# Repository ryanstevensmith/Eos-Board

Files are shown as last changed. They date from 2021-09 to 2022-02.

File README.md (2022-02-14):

# Eos-Board
 The Eos altimeter board for altimeter development within HRG
 
 Due to be built and tested in October 2021
 
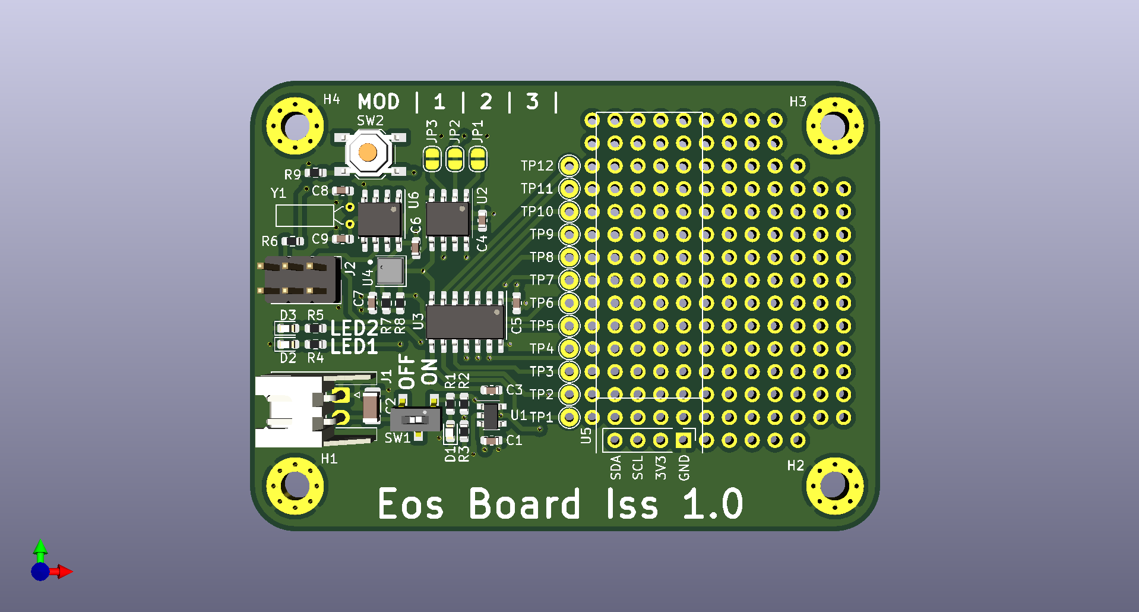
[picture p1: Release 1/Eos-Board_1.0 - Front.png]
image of Board front
 
 
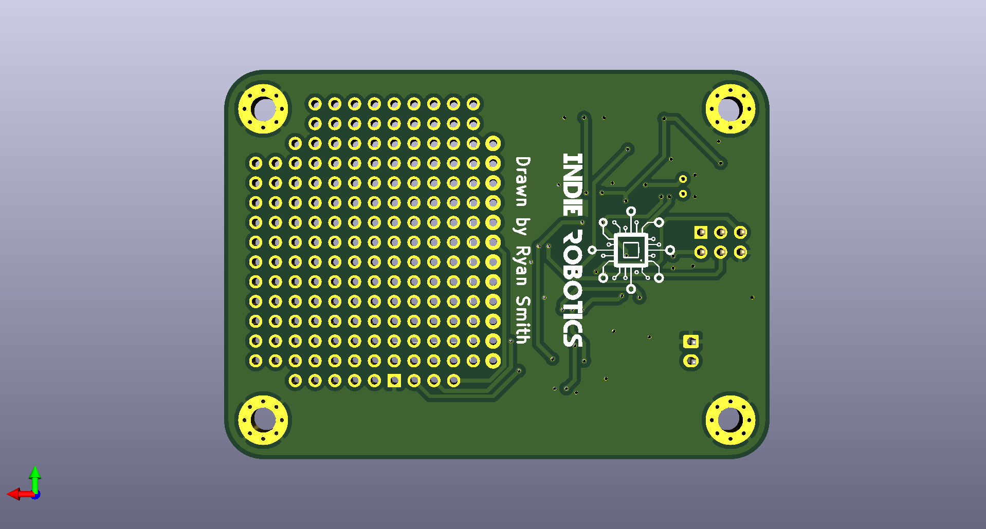
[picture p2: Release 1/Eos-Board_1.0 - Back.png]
image of Board Back
 
 
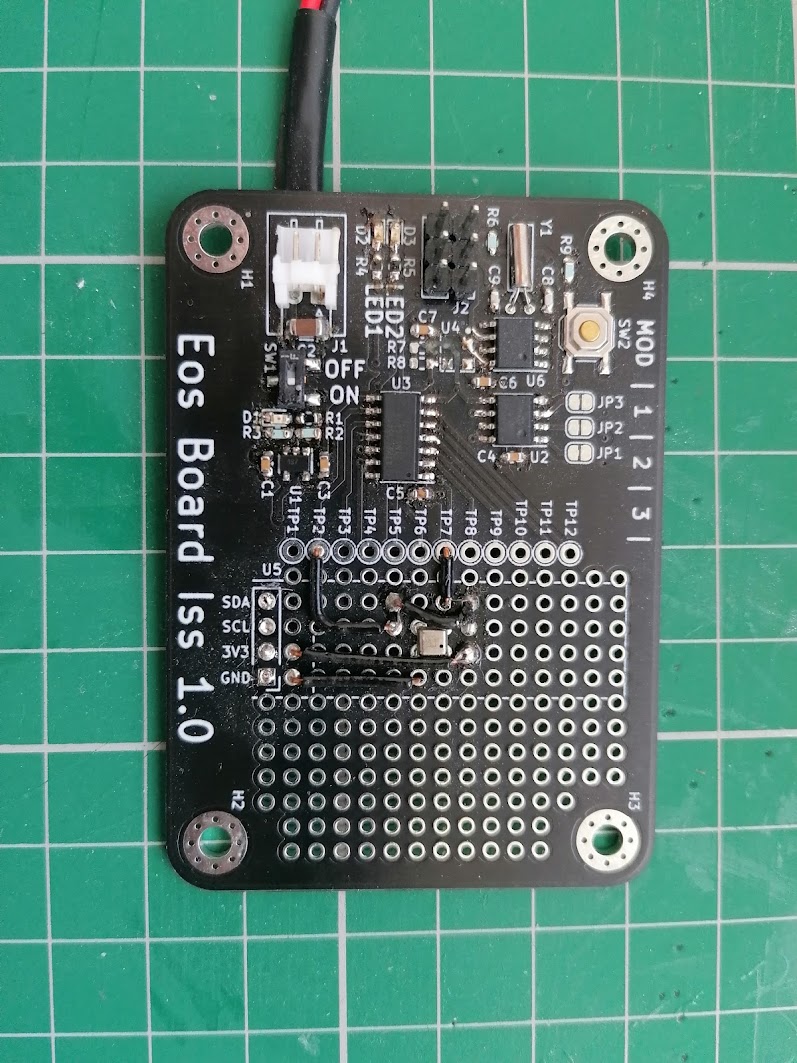
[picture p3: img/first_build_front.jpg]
image of the built board front
 

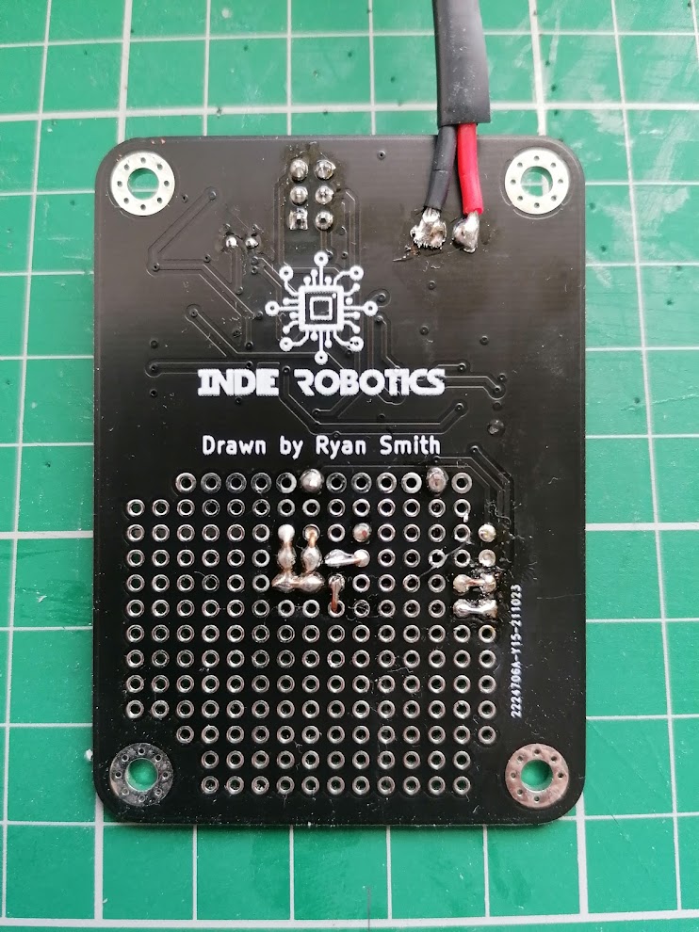
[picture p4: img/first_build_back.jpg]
image of the built board back
 

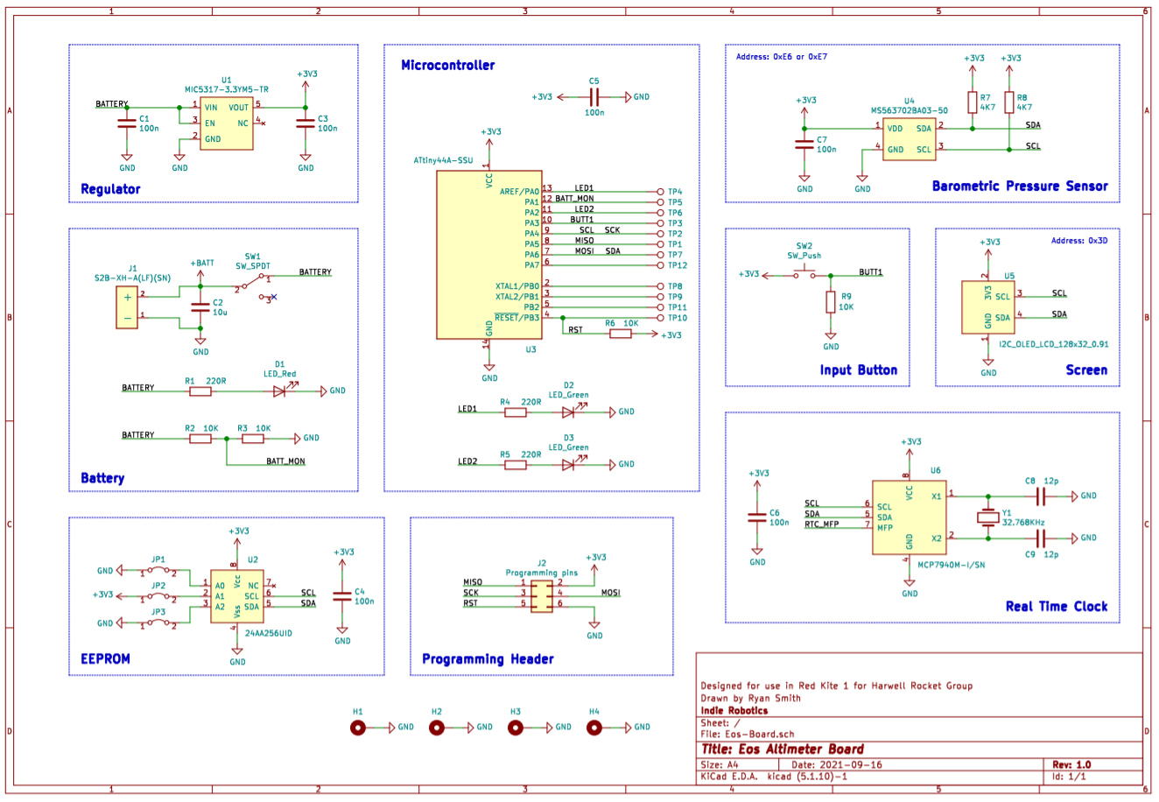
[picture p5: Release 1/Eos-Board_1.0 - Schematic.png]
Schematic Design


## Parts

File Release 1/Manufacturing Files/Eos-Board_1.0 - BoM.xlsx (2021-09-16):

Source: | C:\Users\rsmit\Documents\Rocket Group\Eos-Board\working\Eos-Board.sch
Date: | 2021-09-16
Tool: | Eeschema (5.1.10)-1
Generator: | C:\Program Files\KiCad\bin\scripting\plugins/bom_csv_grouped_by_value.py
Component Count: | 39
Collated Components:
Item | Qty | Reference(s) | Value | Footprint | Part Number | Manufacturer | Description | Datasheet
1 | 6 | C1, C3, C4, C5, C6, C7 | 100n | C_0603_1608Metric | C0603C104J5RACTU | KEMET | 100n, 0603, X7R, 50V | https://api.kemet.com/component-edge/download/specsheet/C0603C104J5RACTU.pdf
2 | 1 | C2 | 10u | C_1206_3216Metric | C1206C106M3PACTU | KEMET | 10u, 1206, X5R, 25V | https://api.kemet.com/component-edge/download/specsheet/C1206C106M3PACTU.pdf
3 | 2 | C8, C9 | 12p | C_0603_1608Metric | C0603C120K5RACTU | KEMET | 10p, 0603, X7R, 50V | https://api.kemet.com/component-edge/download/specsheet/C0603C120K5RACTU.pdf
4 | 1 | D1 | LED_Red | LED_0603_1608Metric | APT1608SRCPRV | Kingbright | Red 0603 LED | https://www.mouser.co.uk/datasheet/2/216/APT1608SRCPRV-226086.pdf
5 | 2 | D2, D3 | LED_Green | LED_0603_1608Metric | APT1608SGC | Kingbright | Green 0603 LED | https://www.mouser.co.uk/datasheet/2/216/APT1608SGC-32861.pdf
7 | 1 | J1 | S2B-XH-A(LF)(SN) | S2B-XH-A(LF)(SN) | S2B-XH-A(LF)(SN) | JST | CONN HEADER R/A 2POS 2.5MM | https://www.te.com/commerce/DocumentDelivery/DDEController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
10 | 3 | R1, R4, R5 | 220R | R_0603_1608Metric | CRCW0603220RFKEAHP | Vishay | 220R, 0603, 1%, 0.33W | https://www.vishay.com/docs/20043/crcwhpe3.pdf
11 | 4 | R2, R3, R6, R9 | 10K | R_0603_1608Metric | CRCW060310K0FKEAHP | Vishay | 10K, 0603, 1%, 0.33W | https://www.vishay.com/docs/20043/crcwhpe3.pdf
12 | 2 | R7, R8 | 4K7 | R_0603_1608Metric | CRCW06034K70FKEAHP | Vishay | 4K7, 0603, 1%, 0.33W | https://www.vishay.com/docs/20043/crcwhpe3.pdf
13 | 1 | SW1 | SW_SPDT | CAS-120-B-type | CAS-120TB | NIDEC | Slide Switch, SPDT, On-On, Surface Mount, CAS Series, 100 mA | https://www.farnell.com/datasheets/2705275.pdf
14 | 1 | SW2 | SW_Push | SW_SPST_TL3342 | TL3342F160QG | E-Switch | Tactile Switches 4.9 X 4.9MM 160G | https://www.mouser.co.uk/datasheet/2/140/TL3342-2065746.pdf
15 | 1 | U1 | MIC5317-3.3YM5-TR | SOT-23-5 | MIC5317-3.3YM5-TR | Microchip | Fixed LDO Voltage Regulator, 2.5V to 6V, 155mV drop, 3.3V/150mA out, SOT-23-5 | http://ww1.microchip.com/downloads/en/DeviceDoc/MIC5317.pdf
16 | 1 | U2 | 24AA256UID | SOIC-8_3.9x4.9mm | 24AA256UID-I/SN | Microchip | EEPROM, 256 Kbit, 32K x 8bit, Serial I2C (2-Wire), 400 kHz, SOIC, 8 Pins | https://4donline.ihs.com/images/VipMasterIC/IC/MCHP/MCHP-S-A0002344565/MCHP-S-A0002344565-1.pdf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
17 | 1 | U3 | ATtiny44A-SSU | SOIC-14_3.9x8.7mm | ATTINY44A-SSU | Microchip | 8 Bit MCU, Low Power High Performance, AVR ATtiny Family ATtiny44 Series Microcontrollers, 20 MHz | http://ww1.microchip.com/downloads/en/DeviceDoc/doc8183.pdf
18 | 1 | U4 | MS563702BA03-50 | MS5637-02BA03 | MS563702BA03-50 | TE | Low Voltage Barometric Pressure Sensor | https://www.te.com/commerce/DocumentDelivery/DDEController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
19 | 1 | U5 | I2C_OLED_LCD_128x32_0.91 | I2C_128x32_OLED_LCD | n/a | n/a | I2C 0.91" LCD OLED screen with SSD1306 driver | https://www.ebay.co.uk/itm/IIC-I2C-0-91-inch-128x32-White-OLED-LCD-Display-Module-3-3v-5v-FOR-AVR-Arduino/313145258645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
20 | 1 | U6 | MCP7940M-I/SN | SOIC-8_3.9x4.9mm_P1.27mm | MCP7940M-I/SN | Microchip | RTC IC, Date Time Format (Date/Month/Year hh:mm:ss), I2C, 1.8 V to 5.5 V, MSOP-8 | http://ww1.microchip.com/downloads/en/devicedoc/20002292b.pdf
21 | 1 | Y1 | 32.768KHz | Crystal_DS26_D2.0mm_L6.0mm_Horizontal | R26-32.768- 12.5 | RALTRON | Crystal, 32.768 kHz, Radial, 6.2mm x 2mm Dia, 12.5 pF, 20 ppm, R26 Series | http://www.ramitechnology.com/products/spec/crystal/crystal-r38_26_145.pdf

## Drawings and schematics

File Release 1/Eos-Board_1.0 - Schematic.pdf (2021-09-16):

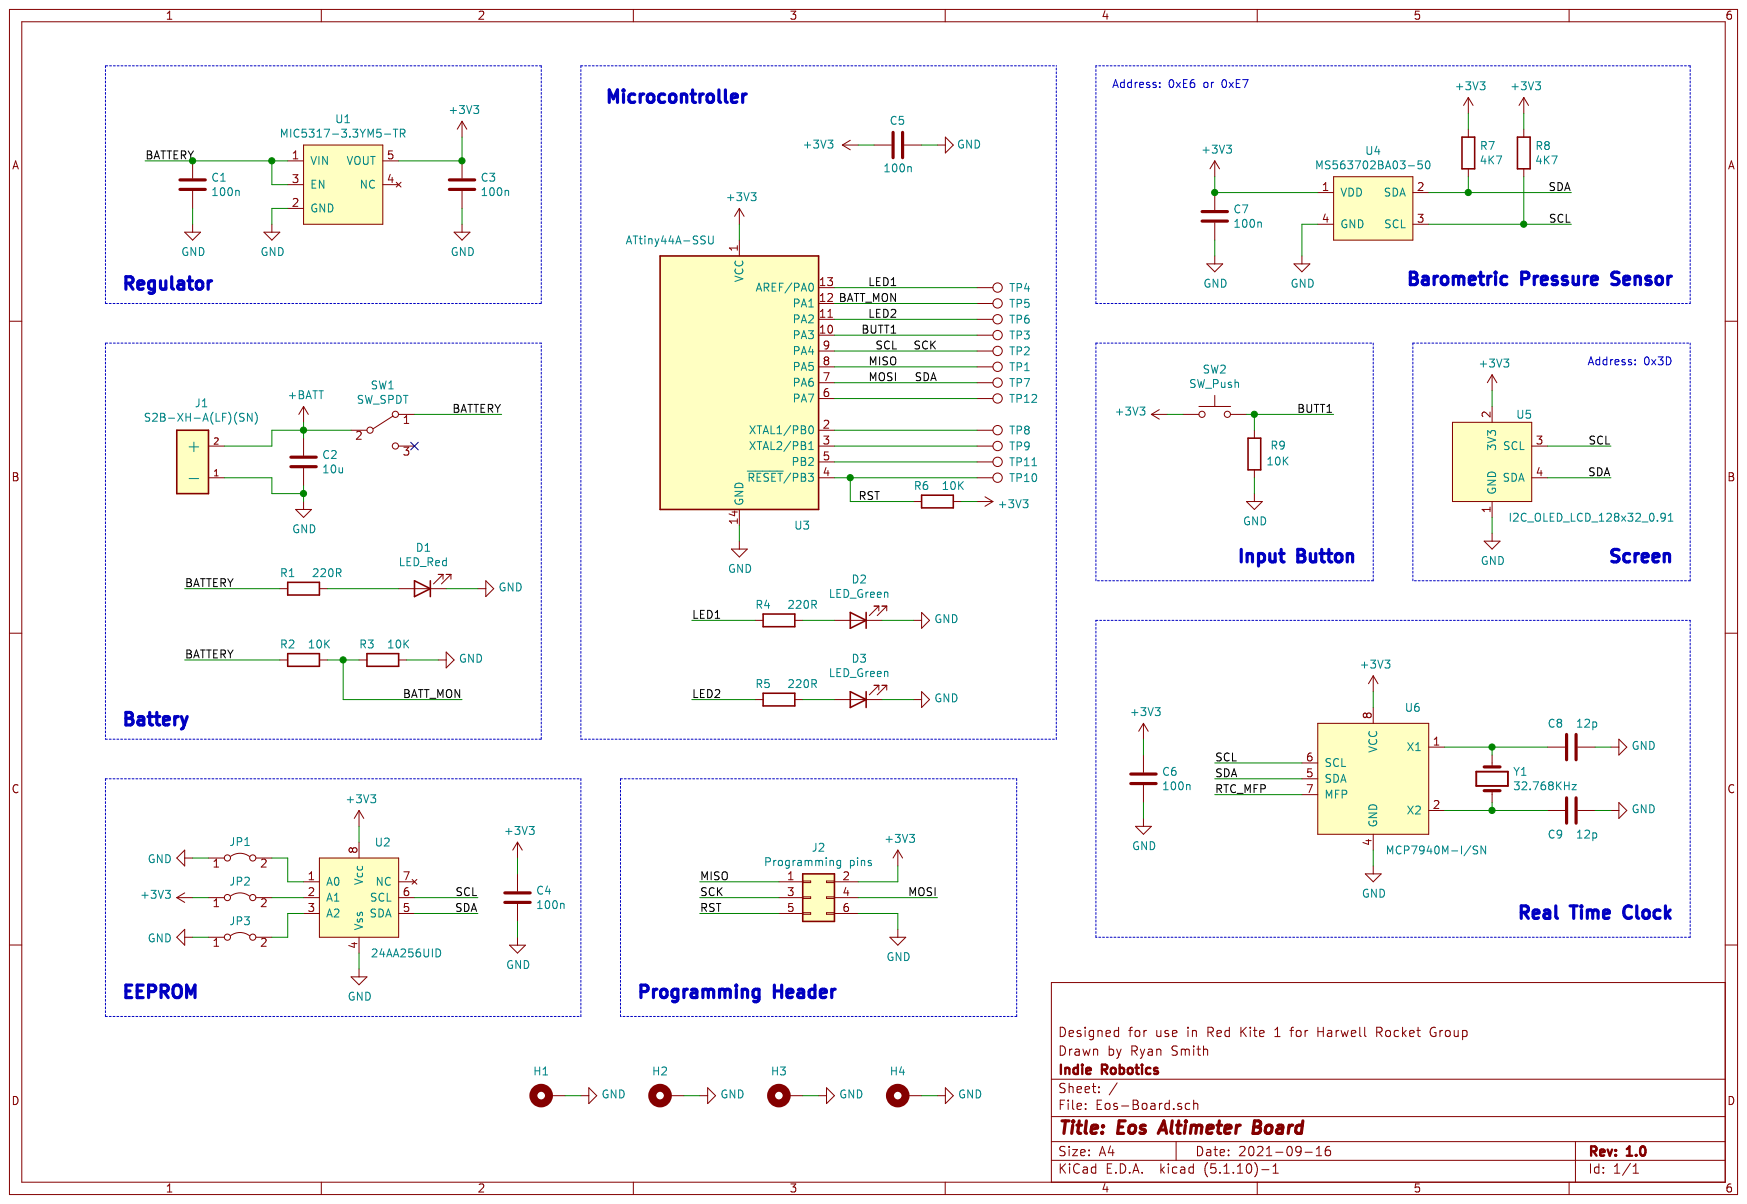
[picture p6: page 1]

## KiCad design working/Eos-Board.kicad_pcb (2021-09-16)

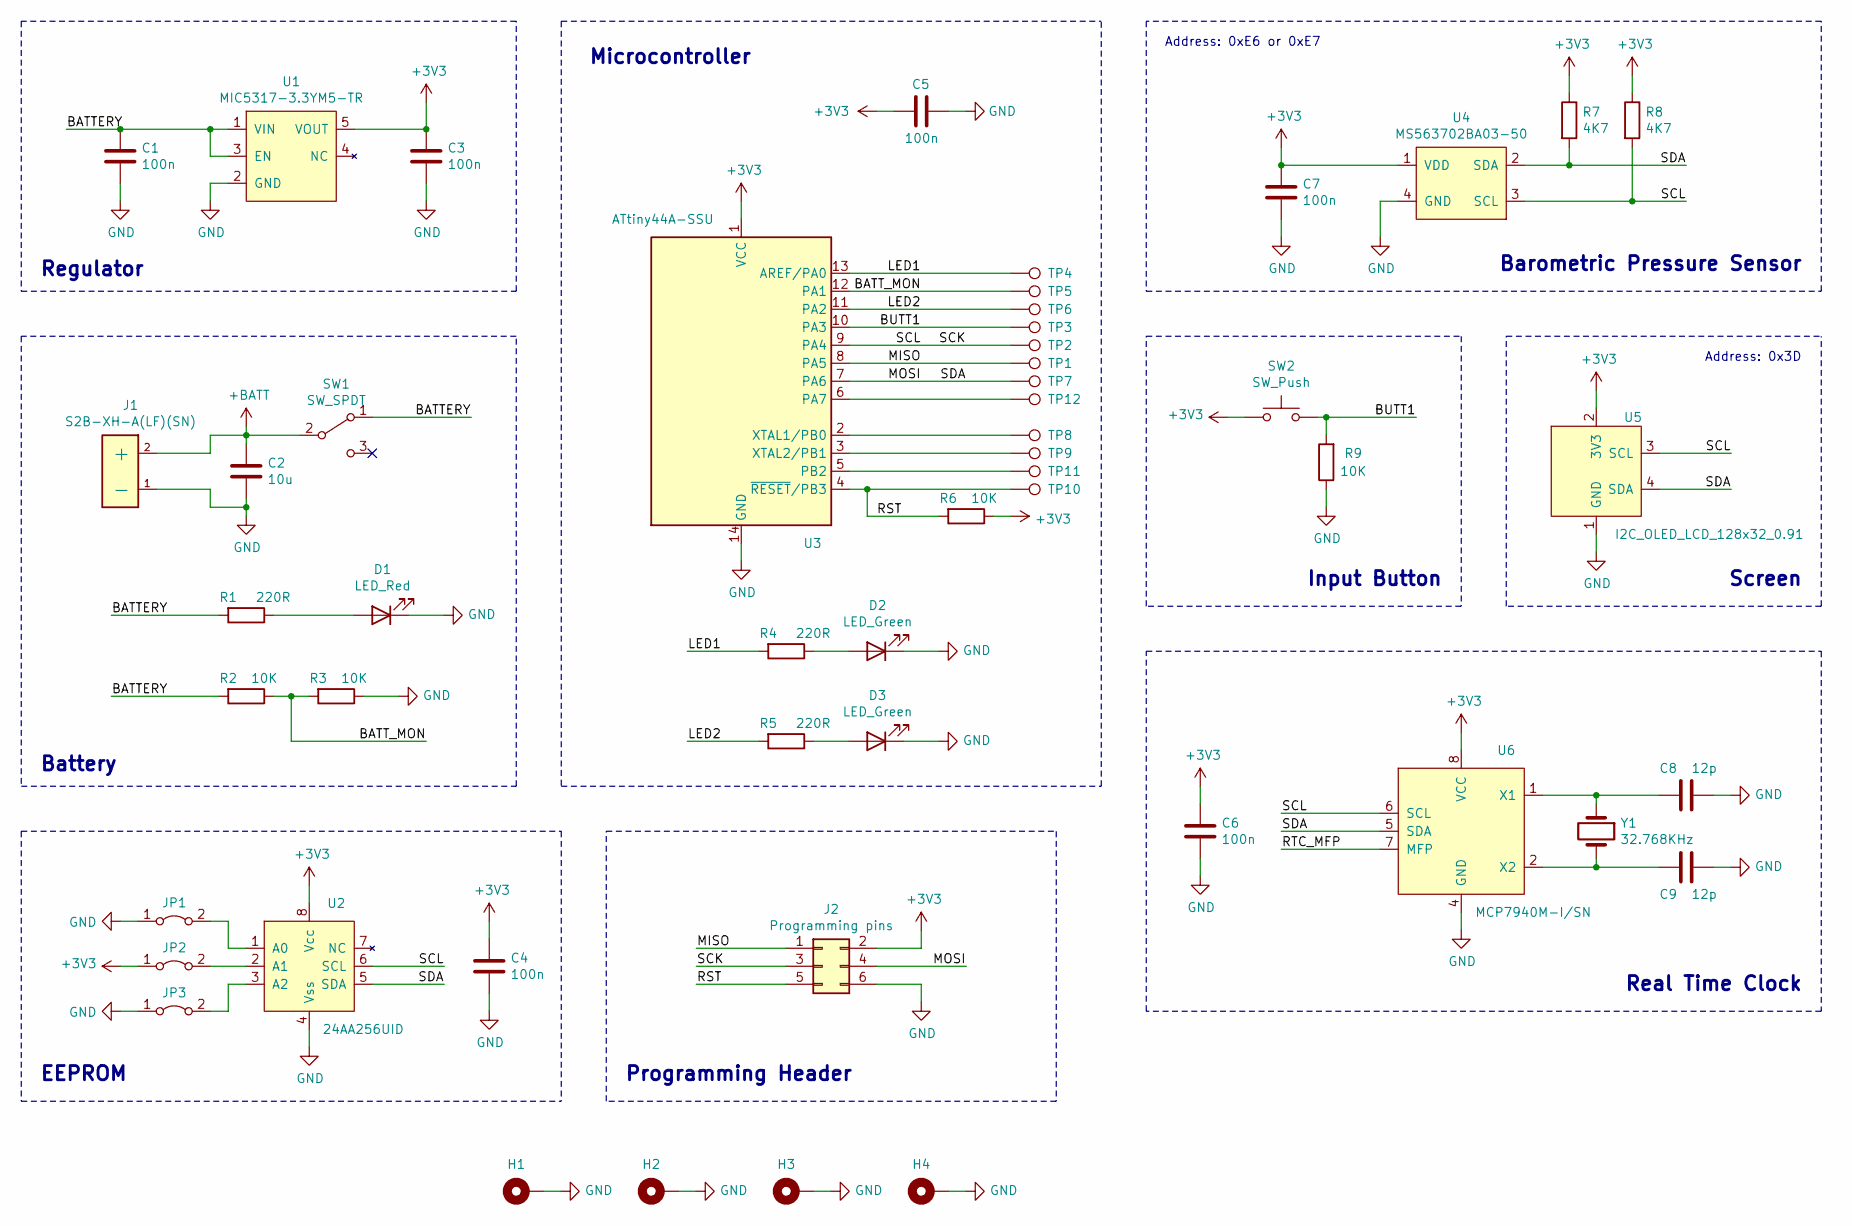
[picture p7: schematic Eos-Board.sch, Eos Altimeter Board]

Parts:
C1, C3, C4, C5, C6, C7: 100n; C_0603_1608Metric; Part Number C0603C104J5RACTU
C2: 10u; C_1206_3216Metric; Part Number C1206C106M3PACTU
C8, C9: 12p; C_0603_1608Metric; Part Number C0603C120K5RACTU
D1: LED_Red; LED_0603_1608Metric; Part Number APT1608SRCPRV
D2, D3: LED_Green; LED_0603_1608Metric; Part Number APT1608SGC
H1, H2, H3, H4: MountingHole_Pad; MountingHole_3.2mm_M3_Pad_Via
J1: S2B-XH-A(LF)(SN); Part Number S2B-XH-A(LF)(SN)
J2: Programming pins; PinHeader_2x03_P2.54mm_Vertical
JP1, JP2, JP3: Jumper_2_Bridged; SolderJumper-2_P1.3mm_Bridged_RoundedPad1.0x1.5mm
R1, R4, R5: 220R; R_0603_1608Metric; Part Number CRCW0603220RFKEAHP
R2, R3, R6, R9: 10K; R_0603_1608Metric; Part Number CRCW060310K0FKEAHP
R7, R8: 4K7; R_0603_1608Metric; Part Number CRCW06034K70FKEAHP
SW1: SW_SPDT; CAS-120-B-type; Part Number CAS-120TB
SW2: SW_Push; SW_SPST_TL3342; Part Number TL3342F160QG
TP1, TP2, TP3, TP4, TP5, TP6, TP7, TP8, TP9, TP10, TP11, TP12: TestPoint; TestPoint_THTPad_D2.0mm_Drill1.0mm
U1: MIC5317-3.3YM5-TR; SOT-23-5; Part Number MIC5317-3.3YM5-TR
U2: 24AA256UID; SOIC-8_3.9x4.9mm_P1.27mm; Part Number 24AA256UID-I/SN
U3: ATtiny44A-SSU; SOIC-14_3.9x8.7mm_P1.27mm
U4: MS563702BA03-50; MS5637-02BA03; Part_Number MS563702BA03-50
U5: I2C_OLED_LCD_128x32_0.91; I2C_128x32_OLED_LCD; Part Number n/a
U6: MCP7940M-I/SN; SOIC-8_3.9x4.9mm_P1.27mm; Part_Number MCP7940M-I/SN
Y1: 32.768KHz; Crystal_DS26_D2.0mm_L6.0mm_Horizontal; Part Number R26-32.768- 12.5

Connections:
+3V3: C3.1, C4.1, C5.1, C6.1, C7.1, J2.2, JP2.1 (A), R6.1, R7.1, R8.1, SW2.1, U1.5 (VOUT), U2.8 (Vcc), U3.1 (VCC), U4.1 (VDD), U5.2 (3V3), U6.8 (VCC)
+BATT: C2.1, J1.2 (+), SW1.2 (B)
/BATTERY: C1.1, R1.2, R2.2, SW1.1 (A), U1.1 (VIN), U1.3 (EN)
/BATT_MON: R2.1, R3.2, TP5.1, U3.12 (PA1)
/BUTT1: R9.2, SW2.2, TP3.1, U3.10 (PA3)
/LED1: R4.2, TP4.1, U3.13 (AREF/PA0)
/LED2: R5.2, TP6.1, U3.11 (PA2)
/MISO: J2.1, TP1.1, U3.8 (PA5)
/MOSI: J2.4, R7.2, TP7.1, U2.5 (SDA), U3.7 (PA6), U4.2 (SDA), U5.4 (SDA), U6.5 (SDA)
/RST: J2.5, R6.2, TP10.1, U3.4 (~RESET~/PB3)
/RTC_MFP: U6.7 (MFP)
/SCK: J2.3, R8.2, TP2.1, U2.6 (SCL), U3.9 (PA4), U4.3 (SCL), U5.3 (SCL), U6.6 (SCL)
GND: C1.2, C2.2, C3.2, C4.2, C5.2, C6.2, C7.2, C8.1, C9.1, D1.1 (K), D2.1 (K), D3.1 (K), H1.1, H2.1, H3.1, H4.1, J1.1 (-), J2.6, JP1.1 (A), JP3.1 (A), R3.1, R9.1, U1.2 (GND), U2.4 (Vss), U3.14 (GND), U4.4 (GND), U5.1 (GND), U6.4 (GND)
unnamed: C8.2, U6.1 (X1), Y1.1
unnamed: C9.2, U6.2 (X2), Y1.2
unnamed: D1.2 (A), R1.1
unnamed: D2.2 (A), R4.1
unnamed: D3.2 (A), R5.1
unnamed: JP1.2 (B), U2.1 (A0)
unnamed: JP2.2 (B), U2.2 (A1)
unnamed: JP3.2 (B), U2.3 (A2)
unnamed: TP8.1, U3.2 (XTAL1/PB0)
unnamed: TP9.1, U3.3 (XTAL2/PB1)
unnamed: TP11.1, U3.5 (PB2)
unnamed: TP12.1, U3.6 (PA7)

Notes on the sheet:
Address: 0xE6 or 0xE7
Address: 0x3D
Regulator
Battery
EEPROM
Programming Header
Microcontroller
Barometric Pressure Sensor
Screen
Real Time Clock
Input Button

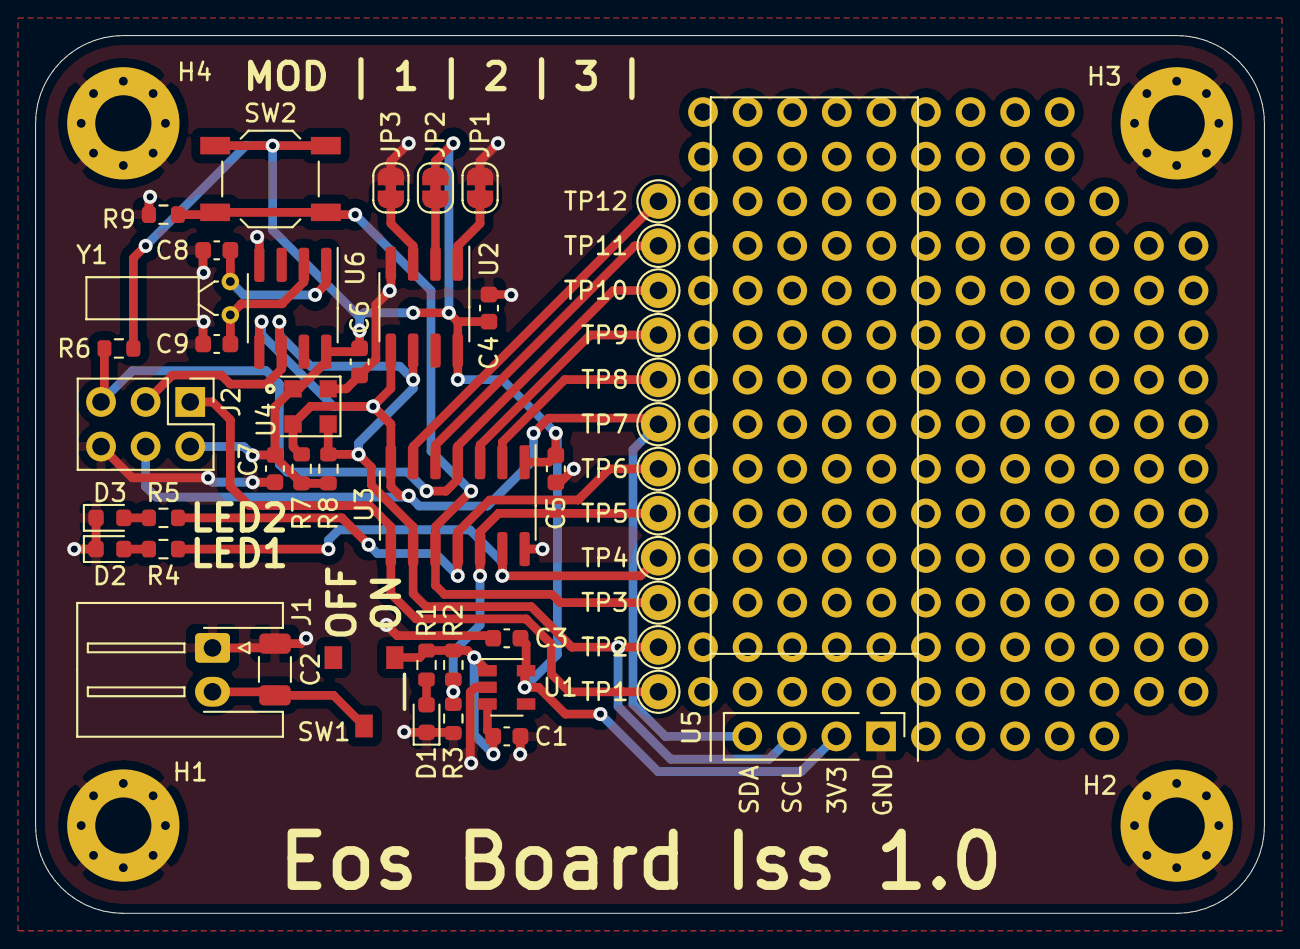
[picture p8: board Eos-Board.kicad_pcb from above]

Board: 2 copper layers, 70.0 x 50.0 mm, 51 parts (0 on the bottom side), 24 nets.

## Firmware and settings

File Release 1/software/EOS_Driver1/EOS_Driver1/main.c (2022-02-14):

/*
 * main.c
 *
 * Created: 11/4/2021 9:51:41 AM
 *  Author: rsmit
 */ 

#include <xc.h>
#include "lib/TinyI2CMaster.h" 


volatile uint16_t time_now = 0;

void __interrupt(TIM1_COMPA_vect_num) isrTim1CompA(void)
{
	TCNT1 = 0;				// Reset counter value
	time_now++;
}

void delay_init(void)
{
	// Setup Timer1
	TCCR1B |= 0x02;				// Set clock prescaler to 8
	TCNT1 = 0;					// Reset counter value
	OCR1A = 100;				// Set compare register A
	TIMSK1 |= (1 << OCIE1A);		// Enable register A compare interrupt
}



int main(void)
{
	uint16_t time_delay = 0;
	
    // Set inputs and outputs
    DDRA |= (1 << PA0);
	DDRA |= (1 << PA2);
	DDRA &= ~(1 <<PA3);

	// Enable Global Interrupts
	SREG |= (1 << SREG_I);
	
	//delay_init();
	time_delay = 10000;
	
	
    while(1)
    {		
		//if (time_now >= (time_delay))
		//{
			//// Toggle PA0 and PA2 with XOR
			//PORTA ^= (1 << PA0);
			//if ((PINA & 0x08))
			//{
				//PORTA ^= (1 << PA2);
			//}
		// time_now = 0;
		//}
		
}

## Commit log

2021-09-16 First Design Files Release
    Initial Release of design files for the design. There should be enough here for a manufacturing run, but not for mass manufacturing.
    [Eos-Board-B_Cu.gbr, Eos-Board-B_Mask.gbr, Eos-Board-B_Paste.gbr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]
2021-09-16 Added schematic image
2021-09-16 Updated Readme
    Added some images of the board render, and an image of the schematic for ease.
